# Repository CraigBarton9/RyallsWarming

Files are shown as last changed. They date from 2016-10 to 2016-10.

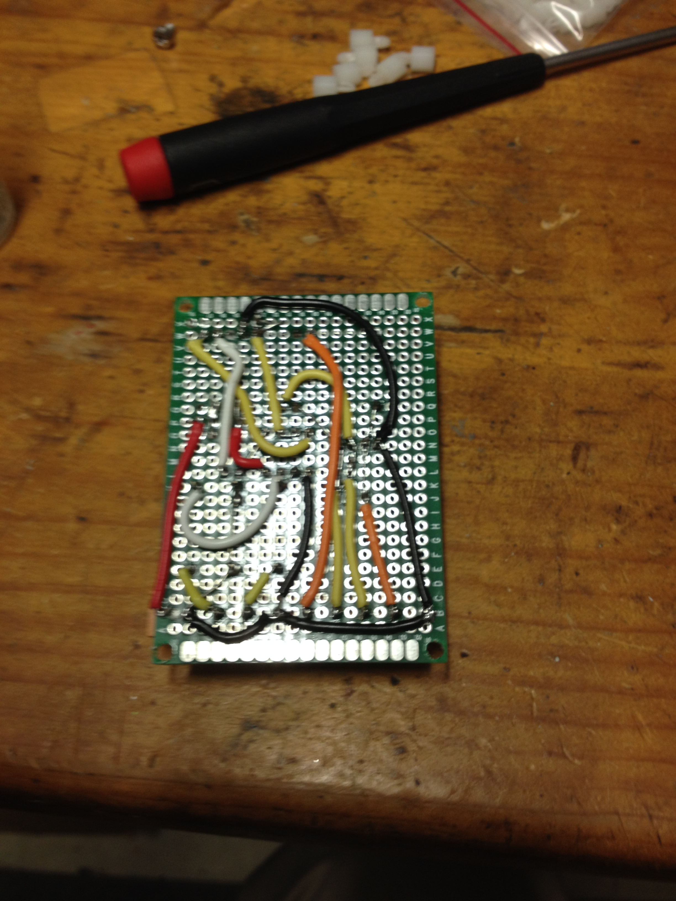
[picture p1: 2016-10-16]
photos/backofboard.JPG

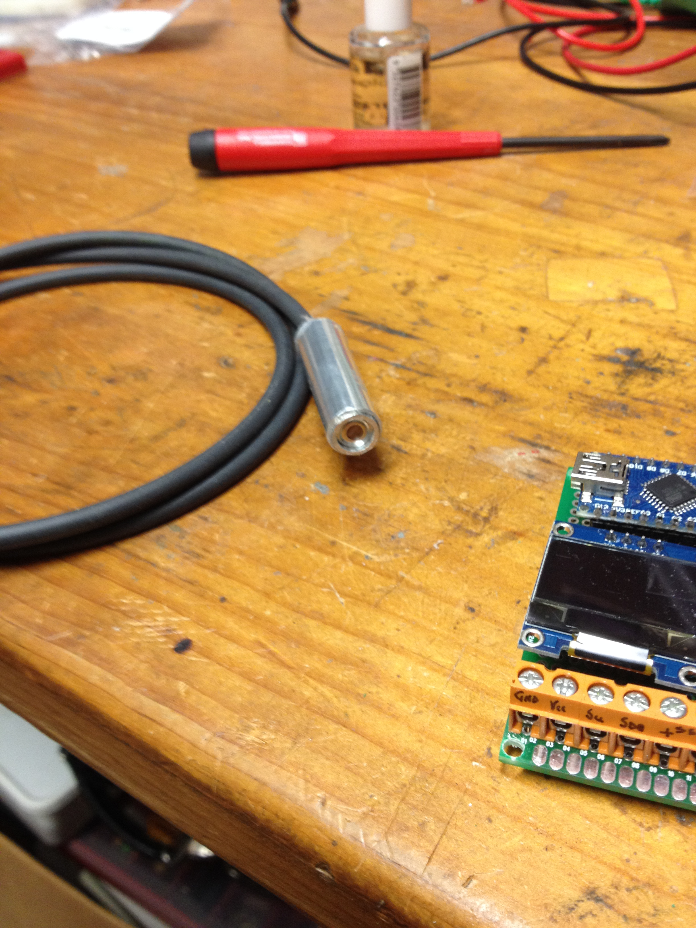
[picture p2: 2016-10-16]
photos/tempsensor1.JPG

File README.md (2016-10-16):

# RyallsWarming
Control system for small radiant warming system
The system comprises of 12 frames 1.5m x 1.5m which are height adjustable. Six of the plots are controls while the other six have 1000W ceramic heat lamps and control units to monitor and regulate the temperature. The control units are built using Arduino Nano micro controllers built as modbus slaves. Each controller has an infrared temperature sensor which monitors the surface temperature of the target 1m2 of the plot. A central control module (Campbell CR1000 data logger) polls each plot to obtain its temperature. It calculates the average of the ambient plots then sends each warmed plot a setpoint value (usually ambient + an offset). The individual plot controllers attempt to regulate the plot temperature by varying the power to its heater using a PID control loop and PWM of the power to the heater via a solid state relay.

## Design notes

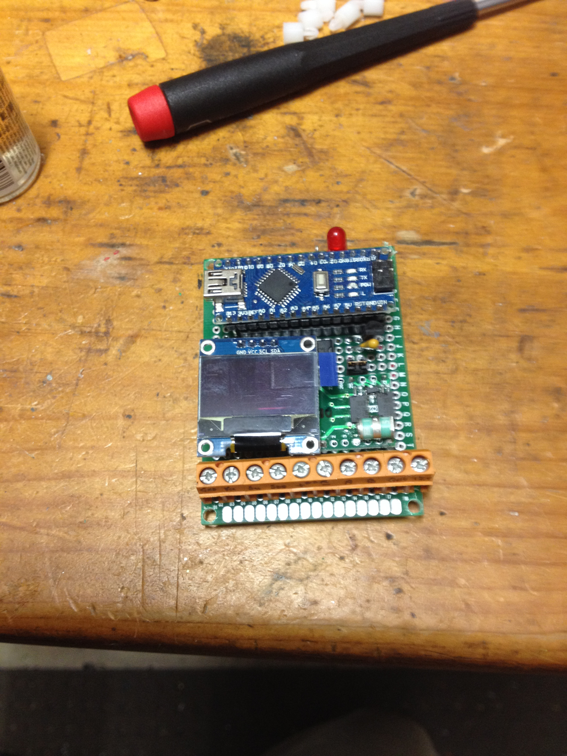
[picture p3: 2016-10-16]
photos/frntofboard.JPG

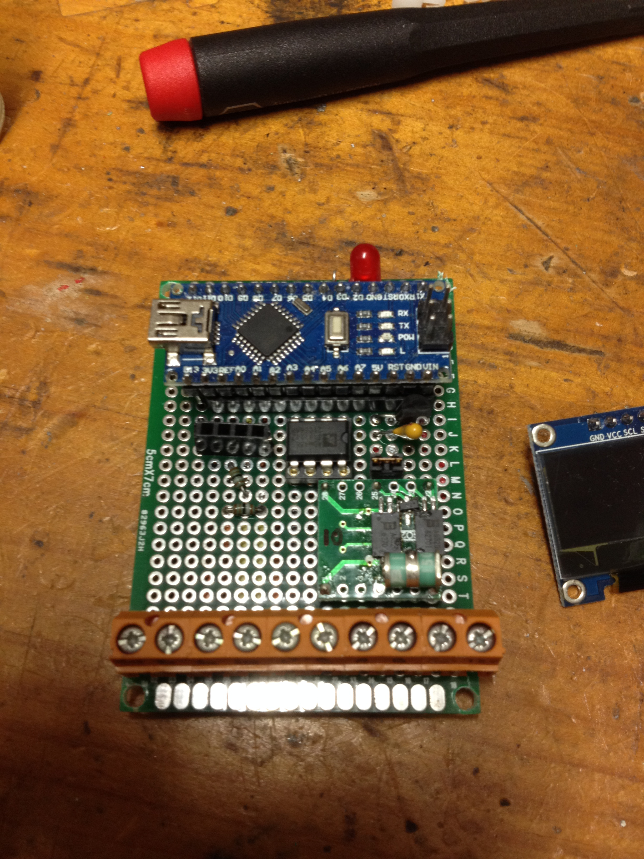
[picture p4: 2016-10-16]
photos/frntofboard2.JPG

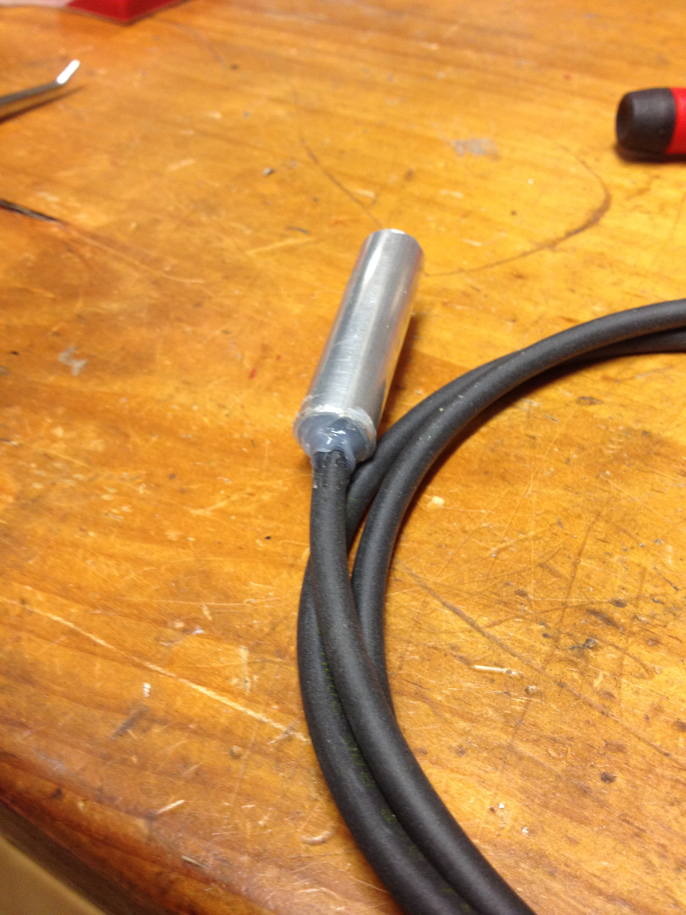
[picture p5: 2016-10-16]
photos/tempsensor2.JPG

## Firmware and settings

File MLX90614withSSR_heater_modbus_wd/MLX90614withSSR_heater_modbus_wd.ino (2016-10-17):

// heater driver
// arduino Nano reading MLX90614 IR thermometer over i2C
// outputing temperature on D5 using PWM (0-5V = 0-50C) 
// reading setpoint on A7 (0-5V = 0-50C) 
// using PID control on D6 to drive SSR and 1KW heater
// display on OLED i2C display
// Craig Barton modified from a number of sources.
#include <SimpleModbusSlave.h>
#include <i2cmaster.h>
#include <SPI.h>
#include <Wire.h>
#include <Adafruit_GFX.h>
#include <Adafruit_SSD1306.h>
#include <PID_v1.h>
#include <avr/wdt.h>

#define OLED_RESET 4
#define RELAY_PIN 6 //digital out
#define POT_Pin 7 //analog input
#define TempOUT_Pin 5 //pwm digital out

Adafruit_SSD1306 display(OLED_RESET);


const int chipSelect = 10;
#define XPOS 0
#define YPOS 1
#define DELTAY 2

//////////===============================
int modbusaddress=12;
//========================================
//Define Variables we'll be connecting to via Processing
double Setpoint, Input, Output;

// Using the enum instruction allows for an easy method for adding and 
// removing registers. Doing it this way saves you #defining the size 
// of your slaves register array each time you want to add more registers
// and at a glimpse informs you of your slaves register layout.

//////////////// registers of your slave ///////////////////
enum 
{     
  // just add or remove registers and your good to go...
  // The first register starts at address 0
  BODY_TEMP,     
  TARG_TEMP,        
  SETPNT,
  DUTY_CYCLE,
  TOTAL_ERRORS,
  // leave this one
  TOTAL_REGS_SIZE 
  // total number of registers for function 3 and 16 share the same register array
};

unsigned int holdingRegs[TOTAL_REGS_SIZE]; // function 3 and 16 register array
////////////////////////////////////////////////////////////


//Specify the links and initial tuning parameters
double Kp=2, Ki=5, Kd=1;
PID myPID(&Input, &Output, &Setpoint, Kp, Ki, Kd, DIRECT);
unsigned long serialTime; //this will help us know when to talk with processing
int WindowSize = 1000;
unsigned long windowStartTime;

// check OLED display
#if (SSD1306_LCDHEIGHT != 64)
#error("Height incorrect, please fix Adafruit_SSD1306.h!");
#endif

float targT;
float bodyT;

void setup(){
//	Serial.begin(9600);
//	Serial.println("Setup...");
// immediately disable watchdog timer so set will not get interrupted

    wdt_disable(); 
//---------------------------------------------- Set PWM frequency for D5 & D6 -------------------------------
 
//TCCR0B = TCCR0B & B11111000 | B00000001;    // set timer 0 divisor to     1 for PWM frequency of 62500.00 Hz
TCCR0B = TCCR0B & B11111000 | B00000010;    // set timer 0 divisor to     8 for PWM frequency of  7812.50 Hz
//TCCR0B = TCCR0B & B11111000 | B00000011;    // set timer 0 divisor to    64 for PWM frequency of   976.56 Hz (The DEFAULT)
//TCCR0B = TCCR0B & B11111000 | B00000100;    // set timer 0 divisor to   256 for PWM frequency of   244.14 Hz
//TCCR0B = TCCR0B & B11111000 | B00000101;    // set timer 0 divisor to  1024 for PWM frequency of    61.04 Hz
 
 
//---------------------------------------------- Set PWM frequency for D9 & D10 ------------------------------
 
//TCCR1B = TCCR1B & B11111000 | B00000001;    // set timer 1 divisor to     1 for PWM frequency of 31372.55 Hz
//TCCR1B = TCCR1B & B11111000 | B00000010;    // set timer 1 divisor to     8 for PWM frequency of  3921.16 Hz
  TCCR1B = TCCR1B & B11111000 | B00000011;    // set timer 1 divisor to    64 for PWM frequency of   490.20 Hz (The DEFAULT)
//TCCR1B = TCCR1B & B11111000 | B00000100;    // set timer 1 divisor to   256 for PWM frequency of   122.55 Hz
//TCCR1B = TCCR1B & B11111000 | B00000101;    // set timer 1 divisor to  1024 for PWM frequency of    30.64 Hz
 
//---------------------------------------------- Set PWM frequency for D3 & D11 ------------------------------
 
//TCCR2B = TCCR2B & B11111000 | B00000001;    // set timer 2 divisor to     1 for PWM frequency of 31372.55 Hz
//TCCR2B = TCCR2B & B11111000 | B00000010;    // set timer 2 divisor to     8 for PWM frequency of  3921.16 Hz
//TCCR2B = TCCR2B & B11111000 | B00000011;    // set timer 2 divisor to    32 for PWM frequency of   980.39 Hz
  TCCR2B = TCCR2B & B11111000 | B00000100;    // set timer 2 divisor to    64 for PWM frequency of   490.20 Hz (The DEFAULT)
//TCCR2B = TCCR2B & B11111000 | B00000101;    // set timer 2 divisor to   128 for PWM frequency of   245.10 Hz
//TCCR2B = TCCR2B & B11111000 | B00000110;    // set timer 2 divisor to   256 for PWM frequency of   122.55 Hz
//TCCR2B = TCCR2B & B11111000 | B00000111;    // set timer 2 divisor to  1024 for PWM frequency of    30.64 Hz
 
//== MODBUS stuff===
  /* parameters(long baudrate, 
                unsigned char ID, 
                unsigned char transmit enable pin, 
                unsigned int holding registers size)
                
     The transmit enable pin is used in half duplex communication to activate a MAX485 or similar
     to deactivate this mode use any value < 2 because 0 & 1 is reserved for Rx & Tx
  */
  
  modbus_configure(&Serial,9600,SERIAL_8N1, modbusaddress, 2, TOTAL_REGS_SIZE,holdingRegs);
  modbus_update_comms(9600, SERIAL_8N2, modbusaddress);
  wdt_enable(WDTO_8S); //watchdog timer set to 8s
//=================  
//  analogReference(DEFAULT);
  pinMode(RELAY_PIN, OUTPUT);      // sets the digital pin as output
  digitalWrite(RELAY_PIN, LOW);
  windowStartTime = millis();
	Input = 15;
  Setpoint = 10;
    //tell the PID to range between 0 and the full window size
  myPID.SetOutputLimits(0, WindowSize);
    //turn the PID on
  myPID.SetMode(AUTOMATIC);
	i2c_init(); //Initialise the i2c bus used to talk to temp sensor and OLED display
	PORTC = (1 << PORTC4) | (1 << PORTC5);//enable pullups
    // by default, we'll generate the high voltage from the 3.3v line internally! (neat!)
  display.begin(SSD1306_SWITCHCAPVCC, 0x3C);  // initialize with the I2C addr 0x3D (for the 128x64)
  // init done
  // Clear the buffer.
  display.clearDisplay();
}

void loop(){
    
    wdt_reset(); //reset watchdog timer
    int dev = 0x5A<<1;
    int data_low = 0;
    int data_high = 0;
    int pec = 0;
    holdingRegs[TOTAL_ERRORS] = modbus_update();
    Setpoint = double(holdingRegs[SETPNT])/100.0;
   //may need to add error checking here
   
  //read the IR temperature sensor data over I2C both target and then sensor body
    i2c_start_wait(dev+I2C_WRITE);
    i2c_write(0x07); //address for temperature of target
    // read
    i2c_rep_start(dev+I2C_READ);
    data_low = i2c_readAck(); //Read 1 byte and then send ack
    data_high = i2c_readAck(); //Read 1 byte and then send ack
    pec = i2c_readNak();
    i2c_stop();
    
    //This converts high and low bytes together and processes temperature, MSB is a error bit and is ignored for temps
    double tempFactor = 0.02; // 0.02 degrees per LSB (measurement resolution of the MLX90614)
    double tempData = 0x0000; // zero out the data
    int frac; // data past the decimal point
    
    // This masks off the error bit of the high byte, then moves it left 8 bits and adds the low byte.
    tempData = (double)(((data_high & 0x007F) << 8) + data_low);
    tempData = (tempData * tempFactor)-0.01;
    
    targT = tempData - 273.15;
    
    // read bodyTa from device
    i2c_start_wait(dev+I2C_WRITE);
    i2c_write(0x06); //address for temperature of sensor body
    
    // read
    i2c_rep_start(dev+I2C_READ);
    data_low = i2c_readAck(); //Read 1 byte and then send ack
    data_high = i2c_readAck(); //Read 1 byte and then send ack
    pec = i2c_readNak();
    i2c_stop();
    
    //This converts high and low bytes together and processes temperature, MSB is a error bit and is ignored for temps
//    double tempFactor = 0.02; // 0.02 degrees per LSB (measurement resolution of the MLX90614)
    tempData = 0x0000; // zero out the data
 //   int frac; // data past the decimal point
    
    // This masks off the error bit of the high byte, then moves it left 8 bits and adds the low byte.
    tempData = (double)(((data_high & 0x007F) << 8) + data_low);
    tempData = (tempData * tempFactor)-0.01;
    
   bodyT = tempData - 273.15;   
   

 //place data on holding registers for comunication to logger
 //convert from float to int after moving 2 dec places.
   holdingRegs[TARG_TEMP]=int(targT*100.0);
   holdingRegs[BODY_TEMP]=int(bodyT*100.0);
   holdingRegs[DUTY_CYCLE]=int(Output);
     
 //display data on the OLED display
   display.clearDisplay();
   display.setTextSize(2);
   display.setTextColor(WHITE);
 //  display.setCursor(0,50);
 //  display.print("Duty :");
 //  display.print((Output/WindowSize)*100,1);   
   display.setCursor(0,0);
   display.print("BodyT:");
   display.print(bodyT,1);
   display.setCursor(0,17);
   display.print("StPnt:");
   display.print(Setpoint,1);  
   display.setCursor(0,35); 
   display.print("TTemp:");
   display.print(targT,1);
   display.setCursor(0,55);
   display.setTextSize(1);
   display.print("addrs ");
   display.print(modbusaddress);
   display.setCursor(60,55); 
   display.print("duty:"); 
   display.print(Output);  
   display.display();
  // rebuild the picture after some delay
  //  delay(500); // wait a second before printing again

  //pid stuff
  Input=targT;
  myPID.Compute();
   /************************************************
   * turn the output pin on/off based on pid output
   ************************************************/
  if (millis() - windowStartTime > WindowSize)
  { //time to shift the Relay Window
    windowStartTime += WindowSize;
  }
  if (Output > millis() - windowStartTime) digitalWrite(RELAY_PIN, HIGH);
  else digitalWrite(RELAY_PIN, LOW);


   
}

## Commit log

2016-10-16 Add files via upload
    added some pictures of the circuit board and temperature sensor.
2016-10-17 arduino program
2016-10-17 add circuit diagram fritzing
    [circuit.fzz]
